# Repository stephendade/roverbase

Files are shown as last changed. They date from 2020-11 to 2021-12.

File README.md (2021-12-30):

# roverbase
A PCB design for Power and Motor control for small robots

This is a PCB design for a robot. It uses 4x 18650 batteries to provide a regulated power supply for electronics, power monitoring and 2x brushed motor controllers.

Todo:
Flip JST-GH power connector
5V power reg - put components closer together
Ext switch option for power switches (W/ESD protection?)
Put power power and power connectors further from battery case
Remove fuse. Look at current limiting FET?
Better alignment of labels

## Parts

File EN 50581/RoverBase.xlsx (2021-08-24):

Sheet: RoverBase
Item | Qty | Reference(s) | MFR | MPN | Min Temp (C) | Max Temp (C) | SPN | SPR | ROHS Compliant? | Supplier Declaration
1 | 1 | BT1 | MPD (Memory Protection Devices) | BK-18650-PC8 | -40 | 180 | BK-18650-PC8-ND | Digikey | RoHS 2. Some RoHS 3 | https://www.memoryprotectiondevices.com/FAQ.php
2 | 1 | C2 | Murata Electronics | GRM155R61A225KE95D | -55 | 85 | 490-10451-1-ND | Digikey | RoHS3 | https://www.murata.com/en-eu/products/capacitor/ceramiccapacitor/certificate
3 | 1 | C1 | Yageo | CC0805KKX7R9BB105 | -55 | 125 | 311-1886-1-ND | Digikey | RoHS3 | https://www.yageo.com/upload/website/yageo_Yageo_MLCC_Rohs_2.0_COC_Sony_SS00259_20210318_21031918_826.pdf
4 | 5 | C3 C5 C7 C19 C20 | Murata Electronics | GRM155R71C104KA88D | -55 | 125 | 490-3261-1-ND | Digikey | RoHS3 | https://www.murata.com/en-eu/products/capacitor/ceramiccapacitor/certificate
5 | 2 | C8 C9 | KEMET | C0603C104Z3VACTU | -30 | 85 | 399-1100-1-ND | Digikey | RoHS3 | https://www.kemet.com/content/dam/kemet/lightning/documents/rohs-and-reach/green-product-roadmap/Response_Directive_2015-863-EU_Amending_2011-65-EU.pdf
6 | 1 | C16 | Nichicon | UWX1C101MCL1GB | -40 | 85 | 493-2105-1-ND | Digikey | RoHS3 | https://products.nichicon.co.jp/en/pdf/XJA043/e-uwx.pdf
7 | 2 | C17 C18 | Panasonic Electronic Components | EEE-1CA100SR | -40 | 85 | PCE3878CT-ND | Digikey | RoHS3 | https://industrial.panasonic.com/cdbs/www-cgi/auto-publishing.cgi?type=ROSU&region=WW&layer=4&cd=ABA0002
8 | 4 | C4 C6 C12 C13 | Murata Electronics | GRM21BR61E106MA73L | -55 | 85 | 490-10748-1-ND | Digikey | RoHS3 | https://www.murata.com/en-eu/products/capacitor/ceramiccapacitor/certificate
9 | 4 | C10 C11 C14 C15 | TDK Corporation | C1608X5R1A226M080AC | -55 | 85 | 445-9077-1-ND | Digikey | RoHS3 | https://product.tdk.com/system/files/dam/doc/product/capacitor/ceramic/mlcc/rohs/mlccrohs_commercial_general_en.pdf
10 | 3 | D1 D2 D3 | Lite-On Inc. | LTST-C193KGKT-5A | -30 | 85 | 160-1828-1-ND | Digikey | RoHS3 | https://optoelectronics.liteon.com/en-global/Page/RoHS
11 | 1 | F1 | Bourns Inc. | MF-RG800-2 | -40 | 85 | 118-MF-RG800-2CT-ND | Digikey | RoHS3 | https://www.bourns.com/docs/Product-Datasheets/mfrg.pdf
12 | 1 | J3 | Wurth Elektronik | 61300411121 | -40 | 105 | 732-5317-ND | Digikey | RoHS3 | https://media.digikey.com/pdf/Other%20Related%20Documents/Wurth/Certificate_of_Compliance_ROHS.pdf
13 | 1 | J2 | JST Sales America Inc. | BM06B-GHS-TBT(LF)(SN)(N) | -25 | 85 | 455-1582-1-ND | Digikey | RoHS2 | https://www.jst.com/wp-content/uploads/2020/12/eGH.pdf
14 | 2 | L1 L2 | Vishay Dale | IHLP3232DZER3R3M01 | -55 | 125 | 541-1373-1-ND | Digikey | RoHS2 | https://www.vishay.com/product?docid=34316&tab=quality
15 | 1 | Q1 | Vishay Siliconix | SQM40081EL_GE3 | -55 | 175 | SQM40081EL_GE3CT-ND | Digikey | RoHS2 | https://www.vishay.com/product?docid=79583&tab=quality
16 | 4 | R1 R12 R13 R14 | Vishay Dale | CRCW04021K00FKEDHP | -55 | 155 | 541-1.00KYCT-ND | Digikey | RoHS2 | https://www.vishay.com/product?docid=20043&tab=quality
17 | 3 | R6 R9 R11 | Vishay Dale | CRCW040210K0FKED | -55 | 155 | 541-3959-1-ND | Digikey | RoHS2 | https://www.vishay.com/product?docid=20035&tab=quality
18 | 1 | R5 | Vishay Dale | CRCW040230K0FKEDC | -55 | 155 | 541-4888-1-ND | Digikey | RoHS2 | https://www.vishay.com/product?docid=20035&tab=quality
19 | 1 | R8 | Vishay Dale | CRCW040256K2FKED | -55 | 155 | 541-5017-1-ND | Digikey | RoHS2 | https://www.vishay.com/product?docid=20035&tab=quality
20 | 1 | R10 | Vishay Dale | CRCW040259K0FKED | -55 | 155 | 541-59.0KLCT-ND | Digikey | RoHS2 | https://www.vishay.com/product?docid=20035&tab=quality
21 | 3 | SW1 SW2 SW3 | C&K | OS102011MA1QN1 | -30 | 70 | CKN9559-ND | Digikey | RoHS3 | https://www.ckswitches.com/wp-content/uploads/2019/10/rohs-reach-compliance-certificate.pdf
22 | 1 | U2 | Allegro MicroSystems | ACS711ELCTR-12AB-T | -40 | 85 | 620-1370-1-ND | Digikey | RoHS3 | https://www.google.com/url?rct=j&q=&esrc=s&cd=
23 | 2 | U5 U6 | Texas Instruments | DRV8838DSGR | -40 | 150 | 296-40081-1-ND | Digikey | RoHS3 | https://www.ti.com/lit/ml/szzq088o/szzq088o.pdf?ts=1616139851771
24 | 2 | U3 U4 | Texas Instruments | TPS565201DDCR | -40 | 125 | 296-49006-1-ND | Digikey | RoHS3 | https://www.ti.com/lit/ml/szzq088o/szzq088o.pdf?ts=1616139851771
25 | 1 | U7 | Texas Instruments | TPS70933DBVT | -40 | 125 | 296-39474-1-ND | Digikey | RoHS3 | https://www.ti.com/lit/ml/szzq088o/szzq088o.pdf?ts=1616139851771

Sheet: Notes
RoHS2 | 2011/65/EU | Required for CE | EN50581
RoHS3 | EU 2015/863

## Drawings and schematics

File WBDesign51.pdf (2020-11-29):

## WEBENCH ® Design Report

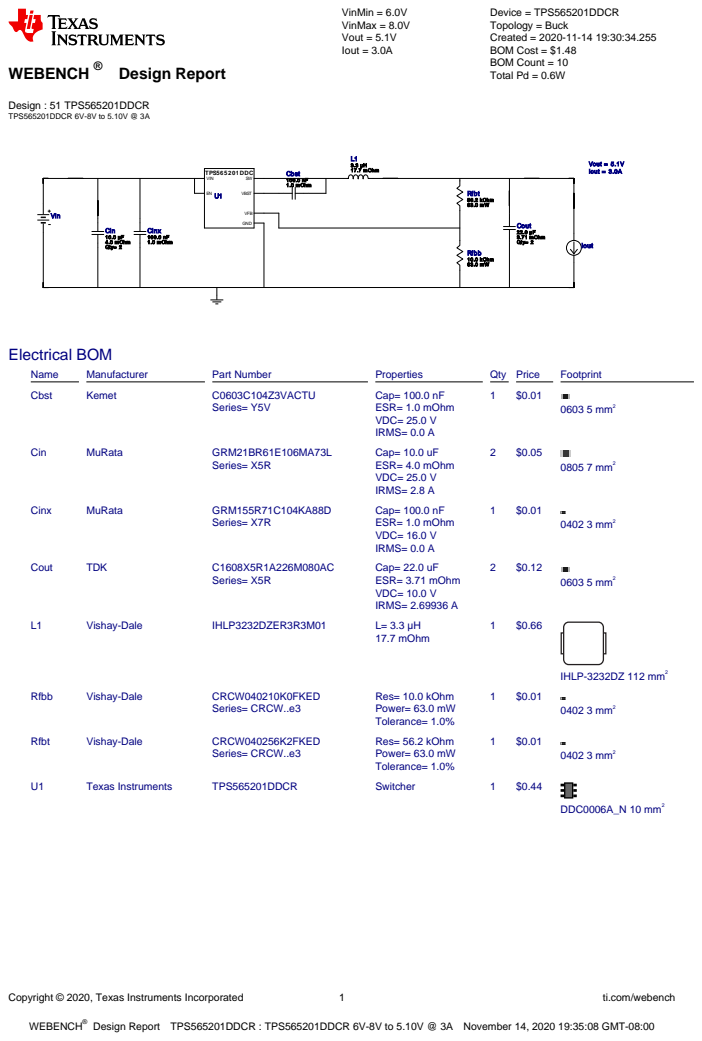
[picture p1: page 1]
Copyright © 2020, Texas Instruments Incorporated; ti.com/webench; WEBENCH®; Design : 51 TPS565201DDCR TPS565201DDCR 6V-8V to 5.10V @ 3A; VinMin = 6.0V VinMax = 8.0V Vout = 5.1V Iout = 3.0A; Device = TPS565201DDCR Topology = Buck Created = 2020-11-14 19:30:34.255 BOM Cost = $1.48 BOM Count = 10 Total Pd = 0.6W; Cbst 100.0 nF 1.0 mOhm; Cin 10.0 µF 4.0 mOhm Qty= 2; Cinx 100.0 nF 1.0 mOhm; Cout 22.0 µF 3.71 mOhm Qty= 2; L1 3.3 µH 17.7 mOhm; Rfbb 10.0 kOhm 63.0 mW; Rfbt 56.2 kOhm 63.0 mW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

Design Report TPS565201DDCR : TPS565201DDCR 6V-8V to 5.10V @ 3A November 14, 2020 19:35:08 GMT-08:00

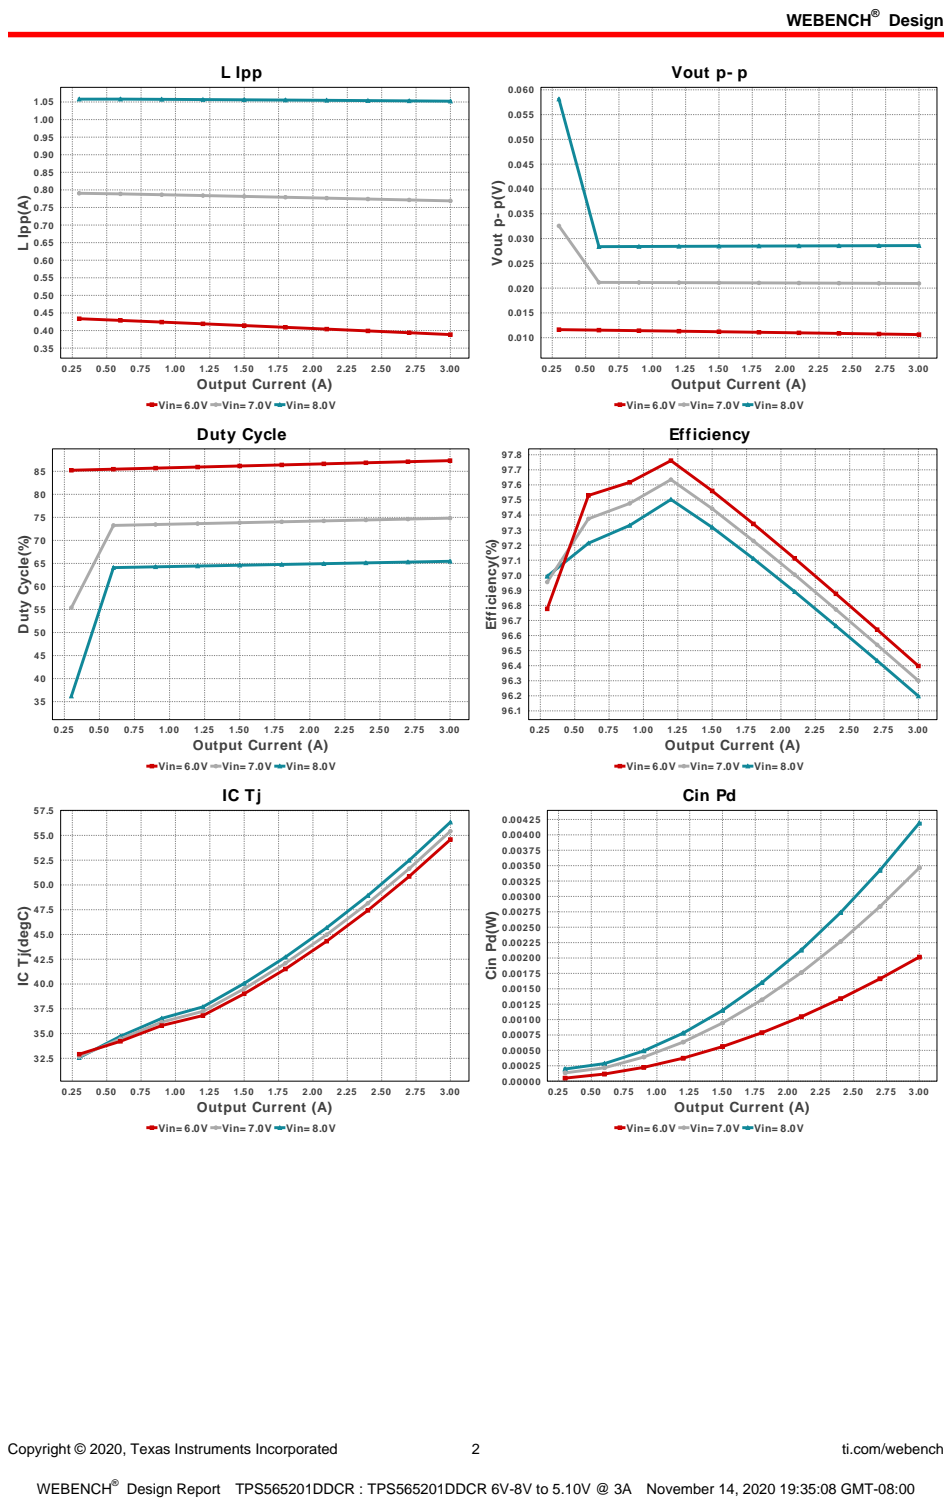
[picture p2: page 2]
Design; Copyright © 2020, Texas Instruments Incorporated; ti.com/webench; L Ipp; 3.00 Output Current (A); L Ipp(A); Vout p- p; Vout p- p(V); Duty Cycle(%); Efficiency(%); 0.25 0.50 0.75 1.00 1.25 1.50 1.75 2.00 2.25 2.50 2.75 3.00 Output Current (A); Cin Pd(W)

Vin= 6.0V Vin= 7.0V Vin= 8.0V
Duty Cycle

Efficiency

Cin Pd

IC Tj(degC)

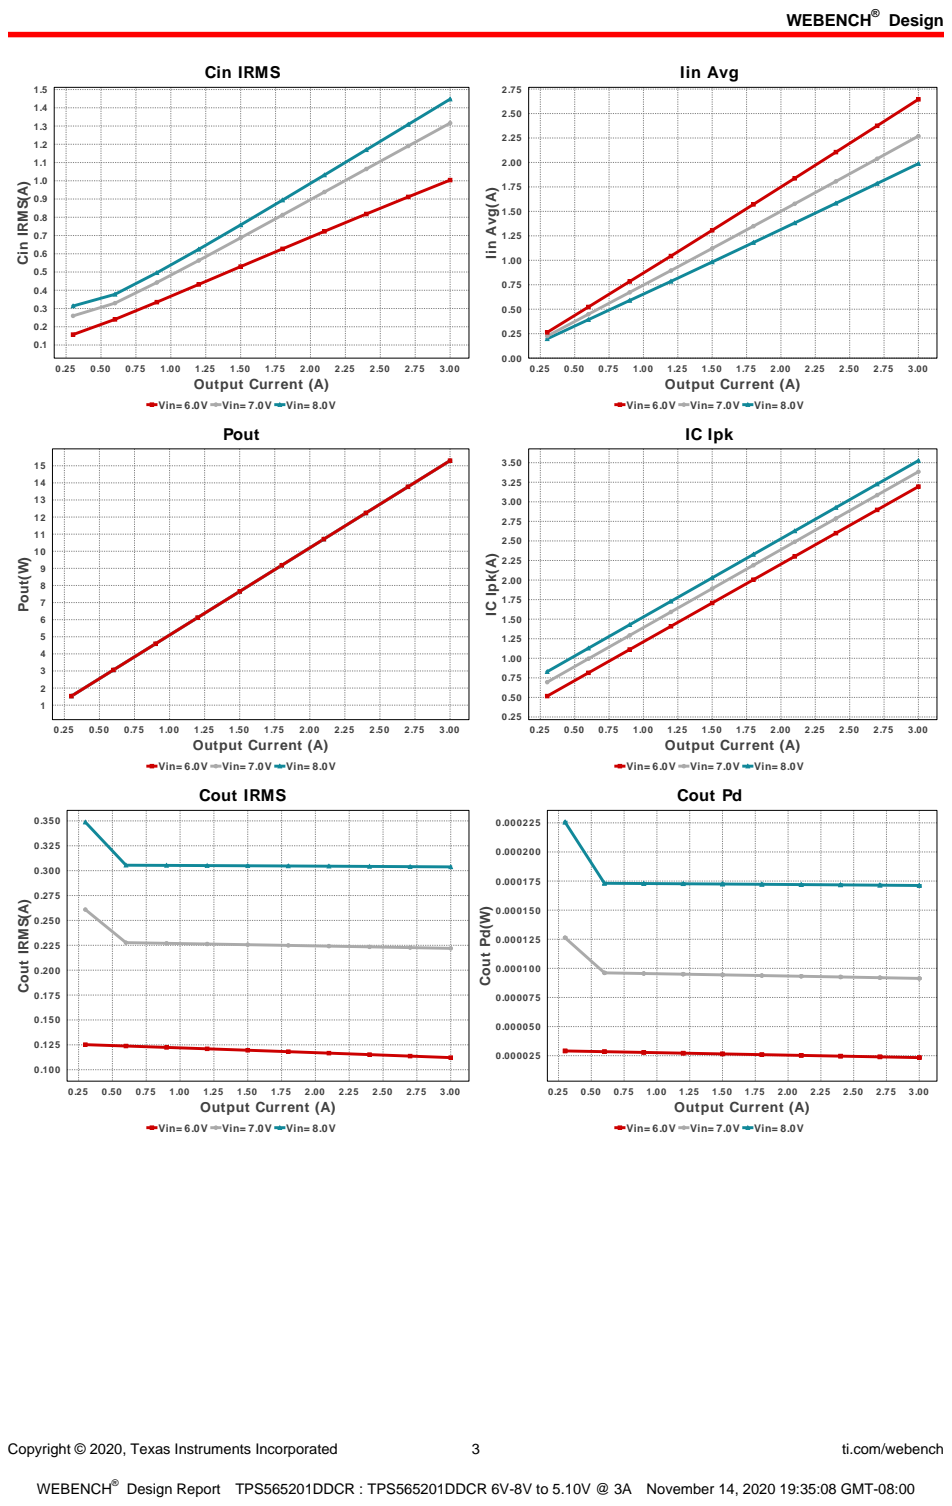
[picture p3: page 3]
Copyright © 2020, Texas Instruments Incorporated; ti.com/webench; Cin IRMS; 3.00 Output Current (A); Cin IRMS(A); Iin Avg; Iin Avg(A); Pout; Pout(W); IC Ipk; IC Ipk(A); Cout IRMS(A); 0.25 0.50 0.75 1.00 1.25 1.50 1.75 2.00 2.25 2.50 2.75 3.00 Output Current (A); Cout Pd(W)

Vin= 6.0V Vin= 7.0V Vin= 8.0V

Cout IRMS

Cout Pd

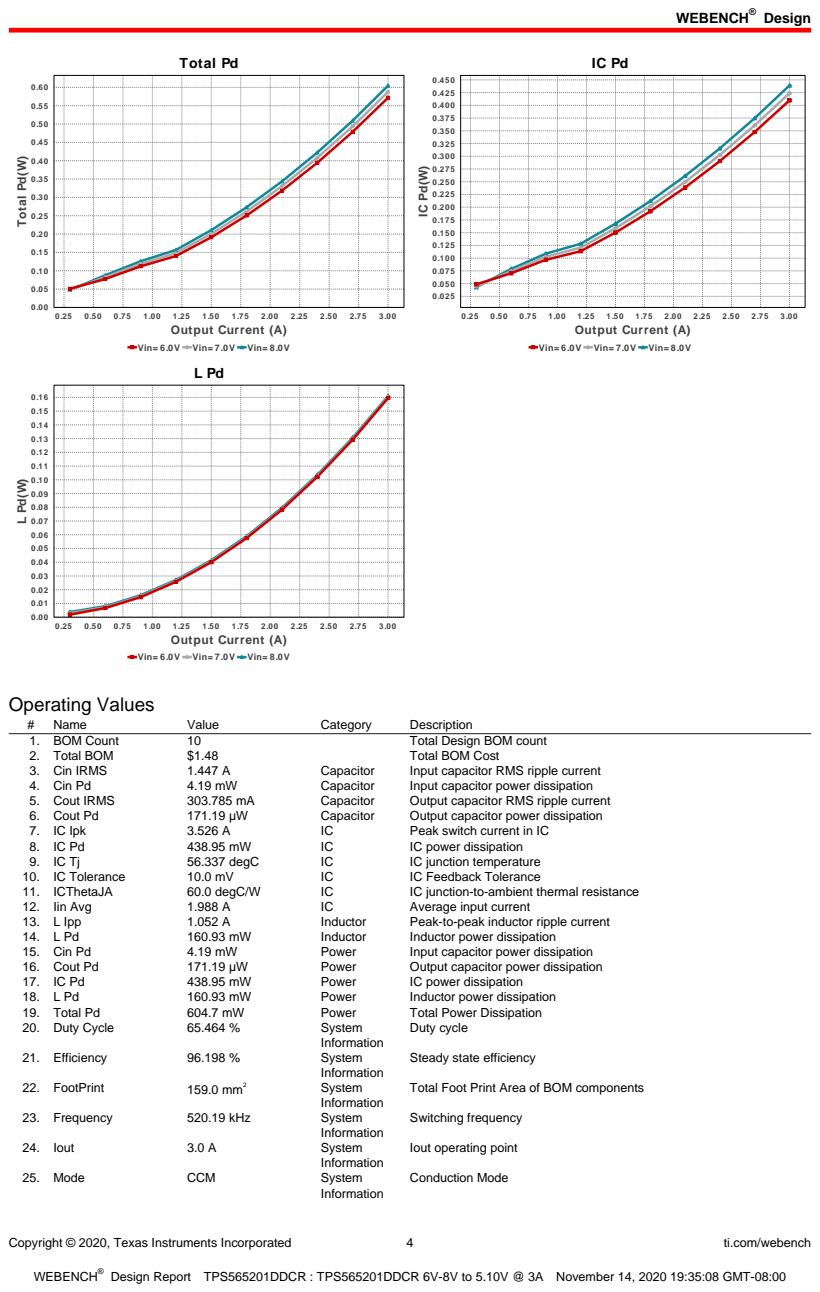
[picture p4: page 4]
Copyright © 2020, Texas Instruments Incorporated; ti.com/webench; Total Pd; 3.00 Output Current (A); Total Pd(W); Operating Values; Name; Value; Category; Description; 1. BOM Count; Total Design BOM count; 2. Total BOM; Total BOM Cost; 3. Cin IRMS; Capacitor; Input capacitor RMS ripple current; 4. Cin Pd; Input capacitor power dissipation; 5. Cout IRMS; Output capacitor RMS ripple current; 6. Cout Pd; Output capacitor power dissipation; 7. IC Ipk; Peak switch current in IC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

Vin= 6.0V Vin= 7.0V Vin= 8.0V

Steady state efficiency

Total Foot Print Area of BOM components

Iout operating point

Copyright © 2020, Texas Instruments Incorporated | 5 | ti.com/webench
# | Name | Value | Category | Description

26. Pout | 15.3 W | System
| | | Information | Total output power
27. Vin | 8.0 V | System
| | | Information | Vin operating point
28. Vout | 5.1 V | System
| | | Information | Operational Output Voltage
29. Vout Actual | 5.064 V | System
| | | Information | Vout Actual calculated based on selected voltage divider resistors
30. Vout Tolerance | 3.045 % | System
| | | Information | Vout Tolerance based on IC Tolerance (no load) and voltage divider resistors if applicable
31. Vout p-p | 28.582 mV | System
| | | Information | Peak-to-peak output ripple voltage

## Design Inputs

Name | Value | Description
Iout | 3.0 | Maximum Output Current
VinMax | 8.0 | Maximum input voltage
VinMin | 6.0 | Minimum input voltage
Vout | 5.1 | Output Voltage
| base_pn | | TPS565201 | Base Product Number
source | DC | Input Source Type
Ta | 30.0 | Ambient temperature


Copyright © 2020, Texas Instruments Incorporated | 6 | ti.com/webench

## Assembly

## Component Testing

Some published data on components in datasheets such as Capacitor ESR and Inductor DC resistance is based on conservative values that will guarantee that the components always exceed the specification. For design purposes it is usually better to work with typical values. Since this data is not always available it is a good practice to measure the Capacitance and ESR values of Cin and Cout, and the inductance and DC resistance of L1 before assembly of the board. Any large discrepancies in values should be electrically simulated in WEBENCH to check for instabilities and thermally simulated in WebTHERM to make sure critical temperatures are not exceeded.

## Soldering Component to Board

If board assembly is done in house it is best to tack down one terminal of a component on the board then solder the other terminal. For surface mount parts with large tabs, such as the DPAK, the tab on the back of the package should be pre-tinned with solder, then tacked into place by one of the pins. To solder the tab town to the board place the iron down on the board while resting against the tab, heating both surfaces simultaneously. Apply light pressure to the top of the plastic case until the solder flows around the part and the part is flush with the PCB. If the solder is not flowing around the board you may need a higher wattage iron (generally 25W to 30W is enough).
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

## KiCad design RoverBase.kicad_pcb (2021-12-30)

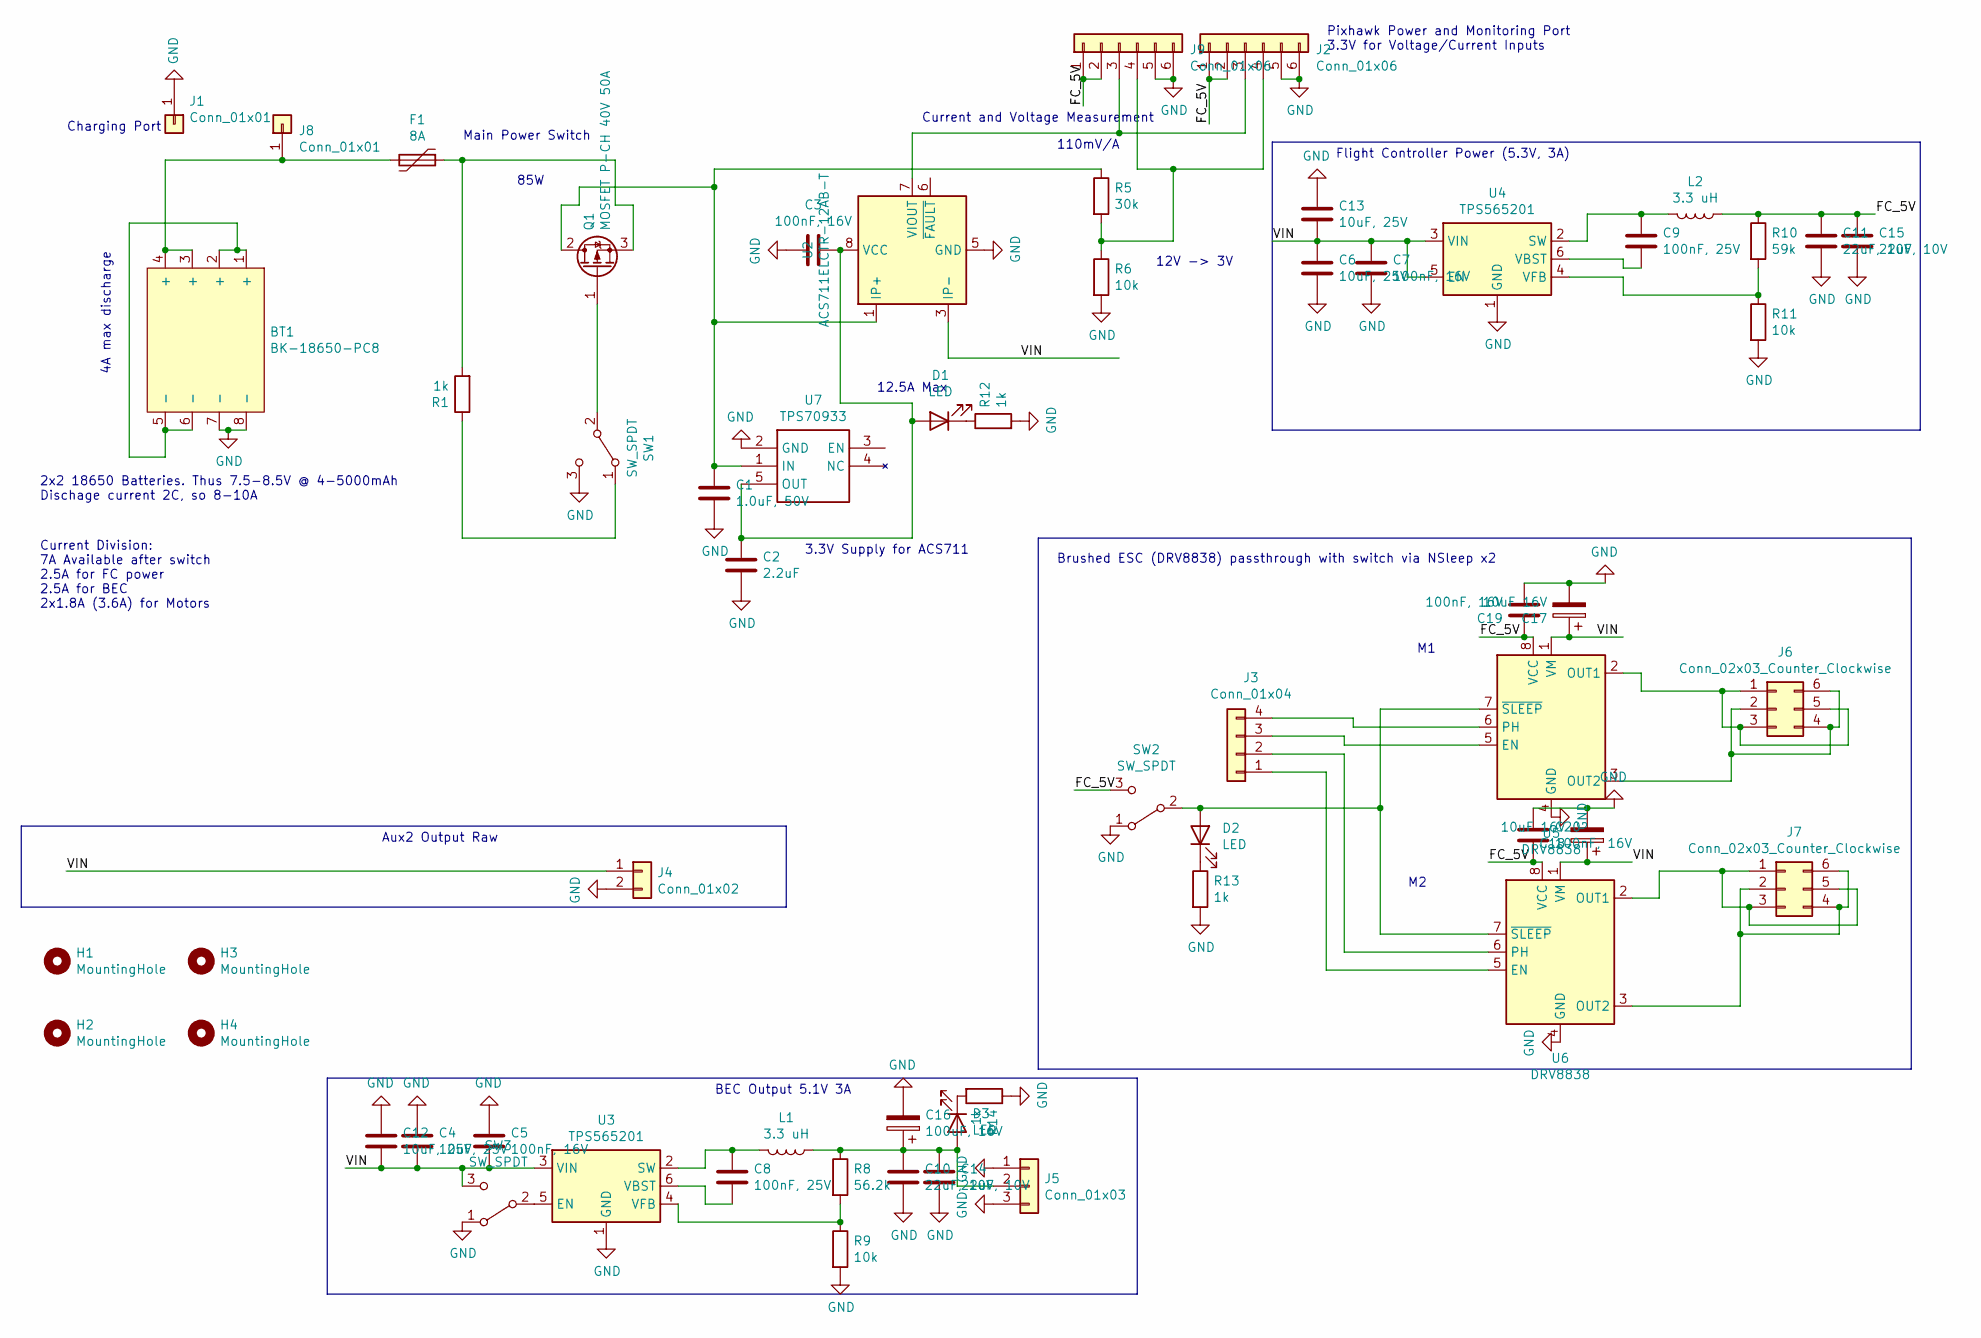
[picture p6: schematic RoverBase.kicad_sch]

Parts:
BT1: BK-18650-PC8; MPN BK-18650-PC8
C1: 1.0uF, 50V; C_0805_2012Metric; MPN CC0805KKX7R9BB105
C2: 2.2uF; C_0402_1005Metric; MPN GRM155R61A225KE95D
C3, C5, C7, C19, C20: 100nF, 16V; C_0402_1005Metric; MPN GRM155R71C104KA88D
C4, C6, C12, C13: 10uF, 25V; C_0805_2012Metric; MPN GRM21BR61E106MA73L
C8, C9: 100nF, 25V; C_0603_1608Metric; MPN C0603C104Z3VACTU
C10, C11, C14, C15: 22uF, 10V; C_0603_1608Metric_Pad1.08x0.95mm_HandSolder; MPN C1608X5R1A226M080AC
C16: 100uF, 16V; CP_Elec_6.3x5.4_Nichicon; MPN UWX1C101MCL1GB
C17, C18: 10uF 16V; CP_Elec_4x5.4; MPN EEE-1CA100SR
D1, D2, D3: LED; LED_0603_1608Metric; MPN LTST-C193KGKT-5A
F1: 8A; Fuse_Bourns_MF-RG800; MPN Bourns Inc.
H1, H2, H3, H4: MountingHole; MountingHole_3.5mm; MPN nf
J1, J8: Conn_01x01; Pin_D1.3mm_L11.0mm; MPN nf
J2: Conn_01x06; JST_GH_BM06B-GHS-TBT_1x06-1MP_P1.25mm_Vertical; MPN BM06B-GHS-TBT(LF)(SN)(N)
J3: Conn_01x04; PinHeader_1x04_P2.54mm_Vertical; MPN 61300411121
J4: Conn_01x02; PinHeader_1x02_P2.54mm_Vertical; MPN nf
J5: Conn_01x03; PinHeader_1x03_P2.54mm_Vertical; MPN nf
J6, J7: Conn_02x03_Counter_Clockwise; PinHeader_2x03_P2.54mm_Vertical; MPN nf
J9: Conn_01x06; PinHeader_1x06_P2.54mm_Vertical; MPN nf
L1, L2: 3.3 uH; L_Vishay_IHLP-3232; MPN IHLP3232DZER3R3M01
Q1: MOSFET P-CH 40V 50A; TO-263-2; MPN SQM40081EL_GE3
R1, R12, R13, R14: 1k; R_0402_1005Metric_Pad0.72x0.64mm_HandSolder; MPN CRCW04021K00FKEDHP
R5: 30k; R_0402_1005Metric_Pad0.72x0.64mm_HandSolder; MPN CRCW040230K0FKEDC
R6, R9, R11: 10k; R_0402_1005Metric_Pad0.72x0.64mm_HandSolder; MPN CRCW040210K0FKED
R8: 56.2k; R_0402_1005Metric_Pad0.72x0.64mm_HandSolder; MPN CRCW040256K2FKED
R10: 59k; R_0402_1005Metric_Pad0.72x0.64mm_HandSolder; MPN CRCW040259K0FKED
SW1, SW2, SW3: SW_SPDT; SW_CuK_OS102011MA1QN1_SPDT_Angled; MPN OS102011MA1QN1
U2: ACS711ELCTR-12AB-T; SOIC-8_3.9x4.9mm_P1.27mm; MPN ACS711ELCTR-12AB-T
U3, U4: TPS565201; SOT-23-6; MPN TPS565201DDCR
U5, U6: DRV8838; WSON-8-1EP_2x2mm_P0.5mm_EP0.9x1.6mm_ThermalVias; MPN DRV8838DSGR
U7: TPS70933; SOT-23-5_HandSoldering; MPN TPS70933DBVT

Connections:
/FC_5V: C11.1, C15.1, C19.1, C20.2, J2.1, J2.2, J9.1, J9.2, L2.1, R10.1, SW2.3 (C), U5.8 (VCC), U6.8 (VCC)
/VIN: C4.2, C5.2, C6.1, C7.1, C12.2, C13.2, C17.1, C18.1, J4.1, SW3.3 (C), U2.3 (IP-), U2.4 (IP-), U3.3 (VIN), U4.3 (VIN), U4.5 (EN), U5.1 (VM), U6.1 (VM)
GND: BT1.7 (-), BT1.8 (-), C1.2, C2.2, C3.2, C4.1, C5.1, C6.2, C7.2, C10.2, C11.2, C12.1, C13.1, C14.2, C15.2, C16.2, C17.2, C18.2, C19.2, C20.1, J1.1, J2.5, J2.6, J4.2, J5.1, J5.3, J9.5, J9.6, R6.2, R9.2, R11.2, R12.2, R13.2, R14.1, SW1.3 (C), SW2.1 (A), SW3.1 (A), U2.5 (GND), U3.1 (GND), U4.1 (GND), U5.4 (GND), U5.9 (GND), U6.4 (GND), U6.9 (GND), U7.2 (GND)
unnamed: BT1.1 (+), BT1.2 (+), BT1.5 (-), BT1.6 (-)
unnamed: BT1.3 (+), BT1.4 (+), F1.2, J8.1
unnamed: C1.1, Q1.2 (D), R5.1, U2.1 (IP+), U2.2 (IP+), U7.1 (IN)
unnamed: C2.1, C3.1, D1.2 (A), U2.8 (VCC), U7.5 (OUT)
unnamed: C8.1, L1.2, U3.2 (SW)
unnamed: C8.2, U3.6 (VBST)
unnamed: C9.1, L2.2, U4.2 (SW)
unnamed: C9.2, U4.6 (VBST)
unnamed: C10.1, C14.1, C16.1, D3.2 (A), J5.2, L1.1, R8.1
unnamed: D1.1 (K), R12.1
unnamed: D2.1 (K), R13.1
unnamed: D2.2 (A), SW2.2 (B), U5.7 (~SLEEP), U6.7 (~SLEEP)
unnamed: D3.1 (K), R14.2
unnamed: F1.1, Q1.3 (S), R1.2
unnamed: J2.3, J9.3, U2.7 (VIOUT)
unnamed: J2.4, J9.4, R5.2, R6.1
unnamed: J3.1, U6.5 (EN)
unnamed: J3.2, U6.6 (PH)
unnamed: J3.3, U5.5 (EN)
unnamed: J3.4, U5.6 (PH)
unnamed: J6.1, J6.3, J6.5, U5.2 (OUT1)
unnamed: J6.2, J6.4, J6.6, U5.3 (OUT2)
unnamed: J7.1, J7.3, J7.5, U6.2 (OUT1)
unnamed: J7.2, J7.4, J7.6, U6.3 (OUT2)
unnamed: Q1.1 (G), SW1.2 (B)
unnamed: R1.1, SW1.1 (A)
unnamed: R8.2, R9.1, U3.4 (VFB)
unnamed: R10.2, R11.1, U4.4 (VFB)
unnamed: SW3.2 (B), U3.5 (EN)

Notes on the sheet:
Pixhawk Power and Monitoring Port 3.3V for Voltage/Current Inputs
Aux2 Output Raw
85W
Charging Port
4A max discharge
Main Power Switch
3.3V Supply for ACS711
BEC Output 5.1V 3A
2x2 18650 Batteries. Thus 7.5-8.5V @ 4-5000mAh Dischage current 2C, so 8-10A
Flight Controller Power (5.3V, 3A)
12V -> 3V
Current Division: 7A Available after switch 2.5A for FC power 2.5A for BEC 2x1.8A (3.6A) for Motors
12.5A Max
Brushed ESC (DRV8838) passthrough with switch via NSleep x2
Current and Voltage Measurement
110mV/A

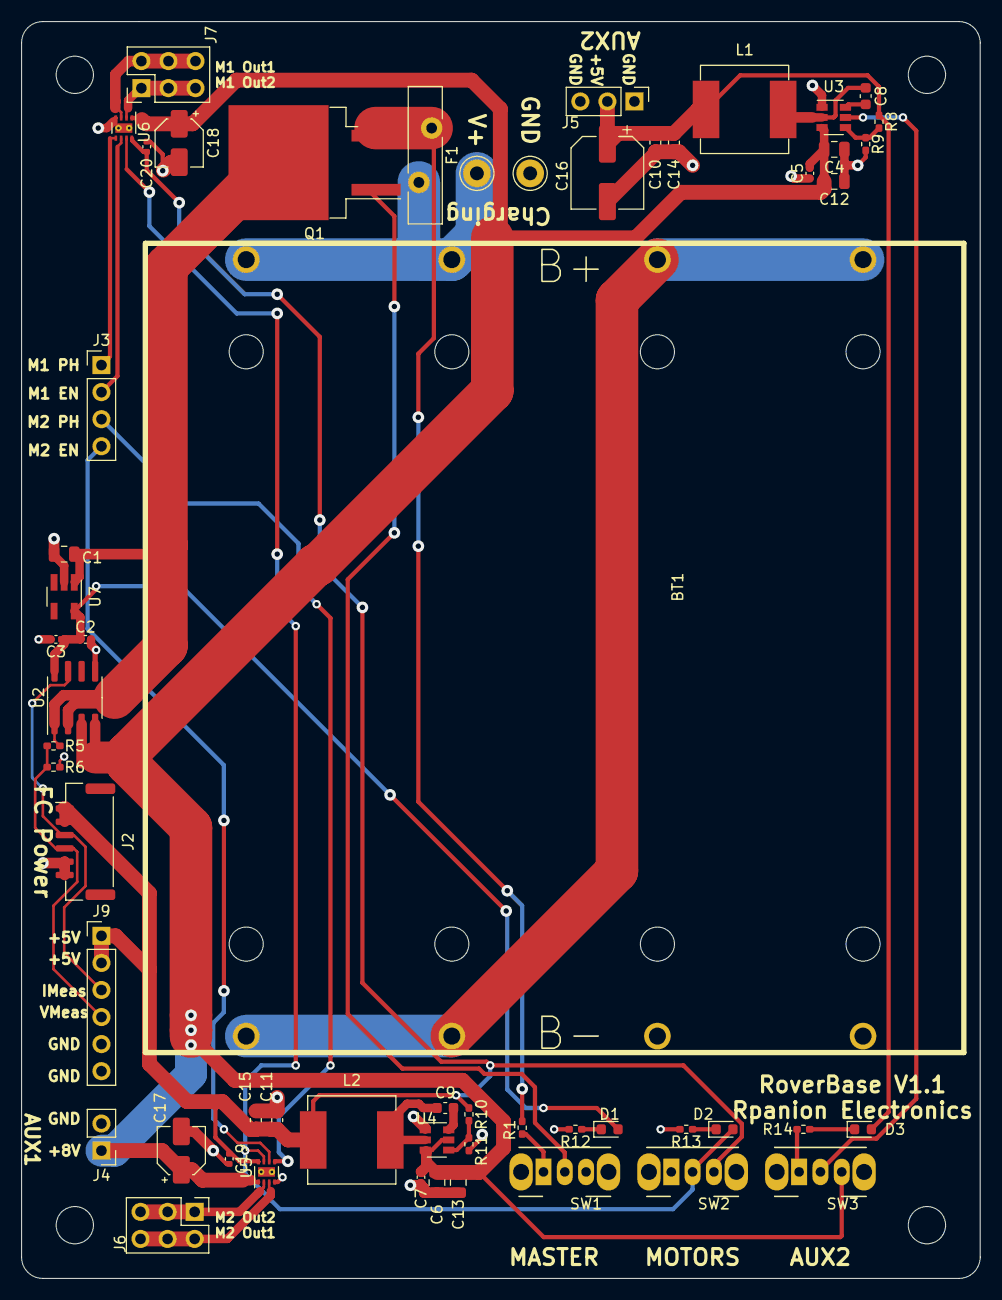
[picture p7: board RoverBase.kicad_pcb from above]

Board: 2 copper layers, 90.0 x 118.0 mm, 60 parts (0 on the bottom side), 32 nets.

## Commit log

2021-01-08 Fixes from V1 testing
    [RoverBase.kicad_pcb, RoverBase.sch]
2021-01-09 Updated inductor footprint
    [RoverBase.kicad_pcb, RoverBase.sch]
2021-01-09 Better power supply placement
    [RoverBase.kicad_pcb, RoverBase.sch]
2021-01-31 Updated motor controllers
    [RoverBase.kicad_pcb, RoverBase.sch]
2021-02-20 Smaller size pcb and re-layout
    [RoverBase.kicad_pcb, RoverBase.sch]
2021-02-23 Update board pins
    [RoverBase.kicad_pcb, RoverBase.sch]
2021-02-23 Added power system diagram
2021-03-01 FC Power 5.1V to 5.3V
    [RoverBase.kicad_pcb, RoverBase.sch]
2021-03-01 Cleanup and consolidate
    [RoverBase.kicad_pcb, RoverBase.sch]
2021-03-19 Remove diodes and add thermal via for motor controllers
    [RoverBase.kicad_pcb, RoverBase.sch]
2021-03-20 RoHS Compliance
    [RoverBase.kicad_pcb, RoverBase.xlsx]
2021-06-17 Using FET and fuse instead of switch
    [RoverBase.kicad_pcb, RoverBase.sch]
2021-08-24 Update RoHS compliance
    [RoverBase.xlsx]
2021-08-24 Minor PCB updates
    [RoverBase.kicad_pcb]
2021-12-30 Upgrade to KiCad6
    [RoverBase.kicad_pcb, RoverBase.kicad_sch, RoverBase.sch]

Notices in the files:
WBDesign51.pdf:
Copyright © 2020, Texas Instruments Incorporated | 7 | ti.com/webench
